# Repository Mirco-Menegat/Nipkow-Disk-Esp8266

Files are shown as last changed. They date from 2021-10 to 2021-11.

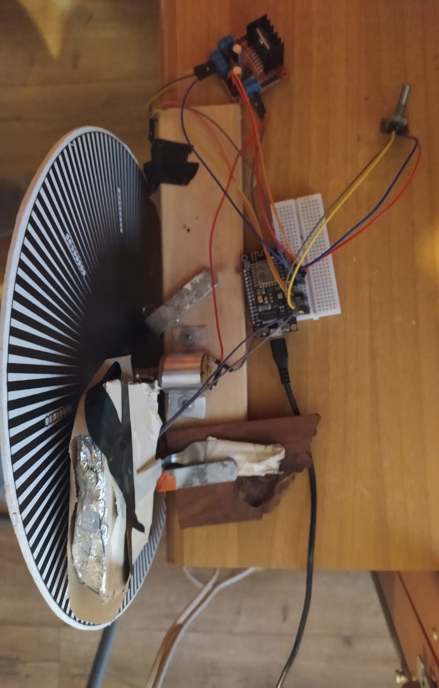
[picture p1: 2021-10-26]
img/foto_disco.jpeg

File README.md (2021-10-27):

# Nipkow-Disk-Esp8266
## Descrizione 
Rivisitazione del disco di Nipkow usando Esp8266. Il disco è in grado di proiettare immagini statiche o un testo scorrevole tramite mqtt.
È stato inserito un rotary encoder siccome solo un ottavo del disco proietta l'immagine corretta, attraverso il rotary encoder possiamo spostare la finestra in modo da averla nella giusta posizione.
Il sensore a infrarossi rileva il passaggio di 128 tacche nere e bianche poste dietro al disco. Un ottavo di queste 128 tacche determinano la risoluzione della larghezza della finestra mentre i numero di fori la risoluzione della sua altezza, quindi il disco ha una risoluzione di 16*8. I buchi e lo spazio tra una tacca e l'altra sono della dimensioni di 3 mm.
L'immagine o la scritta sono contemporaneamente proiettate sul disco e sull'interfaccia grafica in processing.
Se non è proiettata alcuna scritta, cliccando le caselle sull'interfaccia posso disegnare un'immagine.
Premendo alcuni tasti dall'interfaccia ho le seguenti funzionalità:
* 's': se è proiettata una scritta ferma/attiva lo scorrimento della stessa
* 'c': cancella lo schermo
* 'i': se non è proiettata alcuna scritta codifica l'immagine e invia messaggio mqtt all'esp8266 che la proietta sul disco.
## Materiale
* ESP8266
* Disco di Nipkow
* Motore DC 7.5V
* Motor Driver L298N
* led RGB
* Rotary Encoder
* Sensore Infrarossi

## Software ausiliario
* Processing

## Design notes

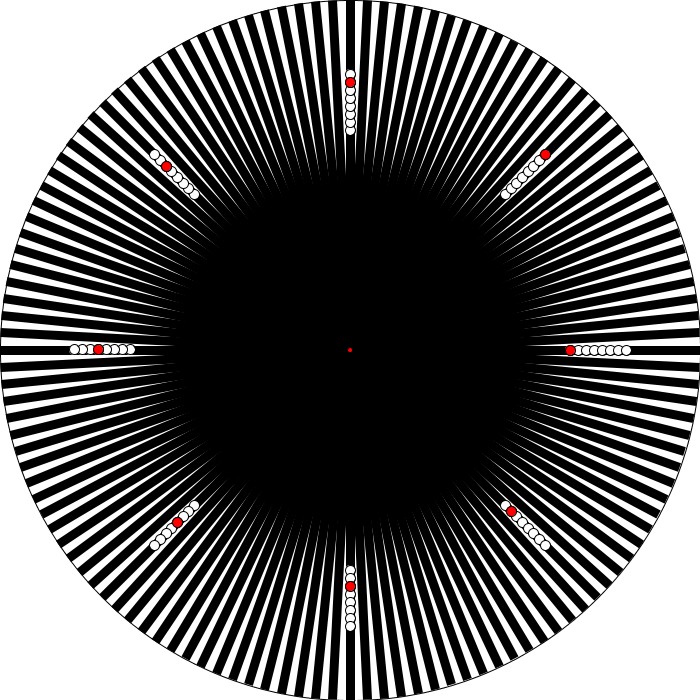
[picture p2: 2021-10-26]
img/nipkow_disk.jpeg

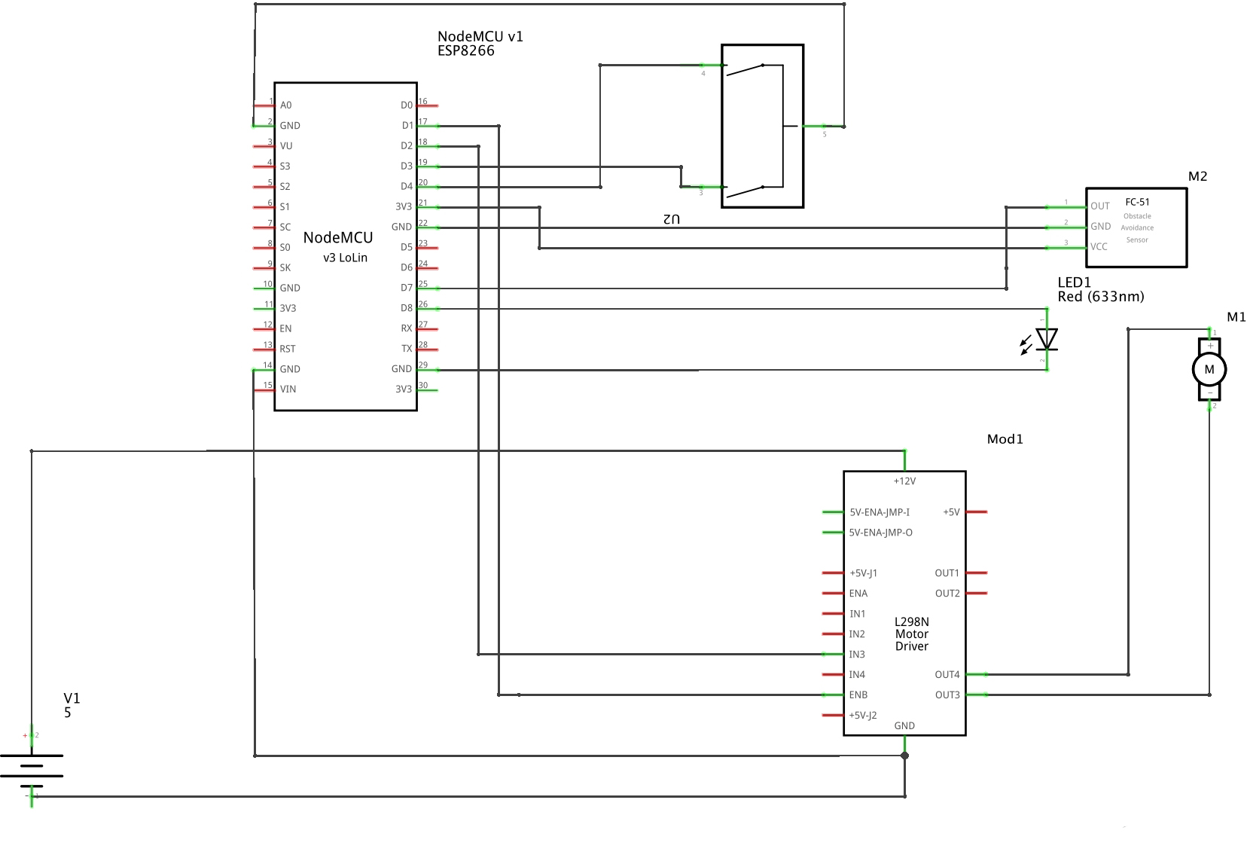
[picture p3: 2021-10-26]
Schema_Circuito.jpg

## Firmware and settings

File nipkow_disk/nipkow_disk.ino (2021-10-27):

#include <ESP8266WiFi.h>
#include <PubSubClient.h>
#include <TaskScheduler.h>
#include<stdio.h>
#include<stdlib.h>
#include <PID_v1.h>
#include "WiFi_Credenziali.h"

#define led D8
#define sensore D7
#define enB  D1
#define in3  D2
#define outputA D3 //DT
#define outputB D4 //CLK


//PID
double Setpoint=580; ; //Rpm ideali
double RPM;
double Output=0 ;
double Kp=2, Ki=10, Kd=0;
double time0_RPM;
double time1_RPM;
PID myPID(&RPM, &Output, &Setpoint, Kp, Ki, Kd, DIRECT);


//STATI DEL ROTARY ENCODER CORRENTE E PRECEDENTE  
int aState;
int aLastState;

// CREDENZIALI WIFI
const char *ssid = ssid_Wifi;
const char *password = password_Wifi;

// MQTT BROKER
const char *mqtt_broker = "broker.hivemq.com";
const char *topic = "/Nipkow_Disk-Esp8266/buffer";
const char *mqtt_username = "esp8266";
const char *mqtt_password = "public";
const int mqtt_port = 1883;

//BUFFER CORRENTE E BUFFER DI RISERVA
boolean sel_buff=false;                         //flag di selezione per selezionare il buffer corrente e quello di riserva
int buff0[128];
int buff_length=8;
int * buff_pointer=buff0;                        //puntatore al buffer corrente così da non dover spostare tutti gli elementi da un buffer all'altro ma solo il puntatore

int buff1[128];
int buff_length_riserva=8;
int nuovo_messaggio=false;                      //indica se è arrivato un nuovo messaggio mqtt

int contatore_buffer=0;                         //Indice elemento del buffer corrente
boolean luce=false;
int offset=0;
float conta_tacche=0;

Scheduler runner;
WiFiClient espClient;
PubSubClient client(espClient);

//Girando il potenziometro a destra o sinistra aumento o diminuisco rispettivamente l'offset, così da girare la finestra in senso orario o antiorario
void gestisci_rotary_encoder() {
        aState = digitalRead(outputA);
        if (aState != aLastState) {               //girando il potenziometro sposto la finestra a in senso orario o antiorario
            if (digitalRead(outputB) != aState ) { //Se ruoto il potenziometro in senso orario
                offset ++;
            } else { //Se ruoto il potenziometro in senso antiorario
                offset--;
            }
        }
       aLastState = aState;
}

//Calcola RPM del disco
void calculate_RPM() {
    if (time1_RPM-time0_RPM!=0) {
        RPM=60000/(time1_RPM-time0_RPM);       //1 minuto/ il tempo che ci mette a fare un giro
    }
}

void pid_loop(){
    myPID.Compute();
    analogWrite(enB,map(Output,0,255,0,1023));
}
void mqtt_loop(){
   client.loop();
}

void stampa() {
    Serial.println(RPM);
}
Task mqttTask(3*TASK_MILLISECOND, TASK_FOREVER,mqtt_loop);
Task pidTask(3*TASK_MILLISECOND, TASK_FOREVER, pid_loop);
Task printTask(5000*TASK_MILLISECOND, TASK_FOREVER, stampa);
Task rotary_encoderTask(10*TASK_MILLISECOND, TASK_FOREVER, gestisci_rotary_encoder);


//Inverte la luce da accesa a spenta o viceversa contatore_buffer diventa l'indice dell'elemento successivo
void inverti_luce(boolean _luce) {
    luce=!luce;
    if (contatore_buffer<buff_length-1) {
        contatore_buffer++;
    }
    switch(luce) {
    case false:
        digitalWrite(led,LOW);
        break;
    case true:
        digitalWrite(led,HIGH);
        break;
    }
}

//Inverte il buffer puntato da buff_pointer, quello di riserva diventa quello corrente e quello corrente diventa di riserva
void inverti_buffer() {
    buff_length=buff_length_riserva;
    switch(sel_buff) {
    case false:
        buff_pointer=buff0;
        break;
    case true:
        buff_pointer=buff1; ;
        break;
    }
}

//Controlla se il disco è all'inizio del giro, spegne la luce e memorizza il tempo di inizio per calcolare gli rpm
boolean check_inizio_giro() {
    if (conta_tacche==offset) {                        //Inizio il giro sempre con luce spenta
        time0_RPM=millis();
        luce=false;
        digitalWrite(led,LOW);
        return true;
    }
    return false;
}

//Controlla se il disco ha completato un giro, dopo aver memorizzato il tempo che ci ha messo a fare un giro calcola gli RPM, e riporta il disco in condizione iniziale
//Se è arrivato un nuovo messaggio mqtt inverti_buffer()
boolean check_fine_giro() {
    if (conta_tacche>=128+offset) {           //mi preparo a scrivere la nuova colonna solo quando ho finito tutto il giro
        time1_RPM=millis();
        calculate_RPM();
        conta_tacche=offset;
        contatore_buffer=0;
        if (nuovo_messaggio==true) {
            inverti_buffer();
        }
        return true;
    }
    return false;
}

//controllo se sono a inizio giro, aumento il conteggio delle tacche,se il conta_tacche coincide con con il prossimo elemento del buffer inverto la luce, controllo se ho finito
//il giro, se l'indice di elemento del buffer è >= della lunghezza del buffer lo riporto a 0.
void ICACHE_RAM_ATTR gestisci_luce() {
    check_inizio_giro();
    conta_tacche++;
    if (buff_length>0 && int(conta_tacche)==buff_pointer[buff_length-1-contatore_buffer]+offset ) { //Se il buffer non è vuoto e conta_tacche coincide con il prossimo elemento del buffer (conto dal fondo)
        inverti_luce(luce);
    }
    check_fine_giro();
    if (contatore_buffer>=buff_length) {
        contatore_buffer=0;
    }
}


// Leggo il payload dal fondo e inserisco i numeri nel buffer di riserva, quando ho finito nuovo_messagio=true e scambio e indico che il buffer di riserva sarà il prossimo
//buffer corrente
void gestisci_nuovo_messaggio(char *topic, byte *payload, unsigned int length) {
    Serial.print("Nuovo messaggio nel topic: ");
    Serial.println(topic);
    Serial.print("Messaggio:");

    int indice=1,numero=0;
    int n_elemento=0;
    for (int i = length-1; i >=0 ; i--) {  //leggo il char * al contrario così da poter ricostruire i numeri ed inserirli nel buffer che non sto usando correntemente

        if(payload[i]!=',') {
            char cifra=(char) payload[i];
            numero+=(cifra-'0')*indice;
            indice*=10;

        } else {
            switch(sel_buff) {
            case true:
                buff0[n_elemento]=numero;
                break;
            case false:
                buff1[n_elemento]=numero;
                break;
            }
            n_elemento++;
            Serial.print(numero);
            Serial.print(" ");
            indice=1;
            numero=0;
        }
    }
    buff_length_riserva=n_elemento;

    Serial.println();
    Serial.println("-----------------------");
    nuovo_messaggio=true;
    sel_buff=!sel_buff;
}

void setup() {
    Serial.begin(115200);
    pinMode(enB, OUTPUT);
    pinMode(in3, OUTPUT);
    pinMode(led,OUTPUT);
    pinMode(sensore,INPUT_PULLUP);
    Serial.begin (115200);
    digitalWrite(in3, HIGH);

    attachInterrupt(
        digitalPinToInterrupt(sensore),
        gestisci_luce,
        RISING
    );
    // connecting to a WiFi network
    WiFi.begin(ssid, password);
    while (WiFi.status() != WL_CONNECTED) {
        delay(400);
        Serial.println("Connecting to WiFi..");
    }
    Serial.println("Connected to the WiFi network");

    //connecting to a mqtt broker
    client.setServer(mqtt_broker, mqtt_port);
    client.setCallback(gestisci_nuovo_messaggio);
    while (!client.connected()) {
        String client_id = "esp8266-client-";
        client_id += String(WiFi.macAddress());
        Serial.printf("The client %s connects to mqtt broker\n", client_id.c_str());
        if (client.connect(client_id.c_str(), mqtt_username, mqtt_password)) {
            Serial.println("Connected to mqtt broker");
        } else {
            Serial.print("failed with state ");
            Serial.print(client.state());
            delay(100);

        }
    }

    client.subscribe(topic);

    runner.init();
    runner.addTask(printTask);
    runner.addTask(rotary_encoderTask);
    runner.addTask(pidTask);
    runner.addTask(mqttTask);
    mqttTask.enable();
    pidTask.enable();
    printTask.enable();
    rotary_encoderTask.enable();
    aLastState = digitalRead(outputA);

    myPID.SetMode(AUTOMATIC);
    //Adjust PID values
    myPID.SetTunings(Kp, Ki, Kd);
}

void loop() {
    runner.execute();
}

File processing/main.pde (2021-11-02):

import mqtt.*;
import java.nio.charset.StandardCharsets;
int pausa_messaggio=1000;
byte [] stringa=null;
boolean scorri=true;
int altezza =8;
int lunghezza=16;
color bianco=color (255);
color rosso=color (255,0,0);
color [] colori={bianco,rosso};
int iterazione;
float time1=0;
int numero_lettera=0;                                                            //indice lettera nella parola
int lunghezza_lettera=0;                                                         //indice colonna della lettera
int transla_count=0;                                                             //quando finisco di scrivere la parola conta le traslazioni finche non è sparita dallo schermo
int Lettera[][]={{}}; 
MQTTClient client;
TEXTBOX userTB;

grid g;


int A[][]={{15,31,47,63,79,95,111,127},{63,127},{63,127},{15,31,47,63,79,95,111,127}};
int B[][]={{15,31,47,63,79,95,111,127},{15,79,127},{15,79,127},{15,31,47,63,95,111,127}};
int C[][]={{15,31,47,63,79,95,111,127},{15,127},{15,127},{15,127}};
int D[][]={{15,31,47,63,79,95,111,127},{15,127},{15,127},{31,47,63,79,95,111}};
int E[][]={{15,31,47,63,79,95,111,127},{15,63,127},{15,63,127},{15,127}};
int F[][]={{15,31,47,63,79,95,111,127},{63,127},{63,127},{127}};
int G[][]={{15,31,47,63,79,95,111,127},{15,127},{15,63,127},{15,31,47,63,127}};
int H[][]={{15,31,47,63,79,95,111,127},{63},{63},{15,31,47,63,79,95,111,127}};
int I[][]={{15,31,47,63,79,95,111,127}};
int J[][]={{15,31,47},{15},{15},{15,31,47,63,79,95,111,127}};
int K[][]={{15,31,47,63,79,95,111,127},{63,95},{47,111},{15,31,127}};
int L[][]={{15,31,47,63,79,95,111,127},{15},{15},{15}};
int M[][]={{15,31,47,63,79,95,111,127},{127},{95,111,127},{127},{15,31,47,63,79,95,111,127}};
int N[][]={{15,31,47,63,79,95,111,127},{111},{95},{79},{15,31,47,63,79,95,111,127}};
int O[][]={{15,31,47,63,79,95,111,127},{15,127},{15,127},{15,31,47,63,79,95,111,127}};
int P[][]={{15,31,47,63,79,95,111,127},{79,127},{79,127},{79,95,111,127}};
int Q[][]={{15,31,47,63,79,95,111,127},{15,127},{15,127},{15,31,47,63,79,95,111,127},{15}};
int R[][]={{15,31,47,63,79,95,111,127},{63,79,127},{47,79,127},{15,31,79,95,111,127}};
int S[][]={{15,79,95,111,127},{15,79,127},{15,79,127},{15,31,47,63,79,127}};
int T[][]={{127},{127},{15,31,47,63,79,95,111,127},{127},{127}};
int U[][]={{15,31,47,63,79,95,111,127},{15},{15},{15,31,47,63,79,95,111,127}};
int V[][]={{47,63,79,95,111,127},{31},{15},{31},{47,63,79,95,111,127}};
int W[][]={{15,31,47,63,79,95,111,127},{15},{15,31,47},{15},{15,31,47,63,79,95,111,127}};
int X[][]={{15,31,47,111,127},{63,95},{79},{63,95},{15,31,47,111,127}};
int Y[][]={{111,127},{95},{15,31,47,63,79},{95},{111,127}};
int Z[][]={{15,31,127},{15,47,127},{15,63,127},{15,79,127},{15,95,111,127}};
int NR[][]={{95,111},{127},{15,47,63,127},{79,127},{95,111}}; //carattere non riconosciuto -> ?

void update(){ //Preparo la griglia alla prossima colonna da inserire
         switch(stringa[numero_lettera]){
                case 'A':Lettera=A;break;
                case 'B':Lettera=B;break;
                case 'C':Lettera=C;break;
                case 'D':Lettera=D;break;
                case 'E':Lettera=E;break;
                case 'F':Lettera=F;break;
                case 'G':Lettera=G;break;
                case 'H':Lettera=H;break;
                case 'I':Lettera=I;break;
                case 'J':Lettera=J;break;
                case 'K':Lettera=K;break;
                case 'L':Lettera=L;break;
                case 'M':Lettera=M;break;
                case 'N':Lettera=N;break;
                case 'O':Lettera=O;break;
                case 'P':Lettera=P;break;
                case 'Q':Lettera=Q;break;
                case 'R':Lettera=R;break;
                case 'S':Lettera=S;break;
                case 'T':Lettera=T;break;
                case 'U':Lettera=U;break;
                case 'V':Lettera=V;break;
                case 'W':Lettera=W;break;
                case 'X':Lettera=X;break;
                case 'Y':Lettera=Y;break;
                case 'Z':Lettera=Z;break;
                default:Lettera=NR;break;
           }
        
              for(int i=0;i<Lettera[lunghezza_lettera].length;i++){
                   g.griglia[Lettera[lunghezza_lettera][i]].col=rosso;
               }      
              
}

void setup(){
 background(0,180,180);
  client = new MQTTClient(this);
  client.connect("mqtt://broker.hivemq.com", "processing");
  size(800,500);
 g =new grid(16,8);
 g.draw_griglia();
   userTB = new TEXTBOX();
   userTB.X = 250;
   userTB.Y = 430;
   userTB.W = 200;
   userTB.H = 35;


}

void draw(){
   
   if(millis()-time1>pausa_messaggio){       
     //background(180,180,40);
      if(scorri==true && stringa!=null){        
          if (transla_count==lunghezza-1){
              numero_lettera=0;
              lunghezza_lettera=0;
              transla_count=0;
          }
          if (numero_lettera<stringa.length){
              if (lunghezza_lettera<Lettera.length){
                  update();
                  lunghezza_lettera++;
              }else{
                  numero_lettera++;
                  lunghezza_lettera=0;
              }
          }else{
              transla_count++;
          }
     g.draw_griglia();
     invia();
     g.transla(); 
     time1=millis();
     }else if(stringa==null){
         g.draw_griglia();
    }
    fill(250, 250, 250);
   textSize(25);
   text("INVIA MESSAGGIO", 20, 455);
   userTB.DRAW();

   strokeWeight(3);
   textSize(12);
   }
   
  
   
}



void invia(){
String codifica_stringa="";
if (g.griglia[0].col==rosso){
    codifica_stringa= codifica_stringa+",";
    codifica_stringa=codifica_stringa+Integer.toString(1);
}
for(int i=1;i<g.altezza*g.larghezza;i++){
  if (g.griglia[i].col!=g.griglia[i-1].col){
    codifica_stringa=codifica_stringa+",";
    codifica_stringa=codifica_stringa+Integer.toString(i+1);}
}
 println(codifica_stringa);
 println();
 client.publish("/Nipkow_Disk-Esp8266/buffer", codifica_stringa);
}


void clientConnected() {
  println("client connected");
  client.subscribe("/Nipkow_Disk-Esp8266/processing");
}

void connectionLost() {
  println("connection lost");
}

void messageReceived(String topic, byte[] payload) {
  transla_count=0;
  lunghezza_lettera=0;
  numero_lettera=0;
  scorri=true;
  String s = new String(payload, StandardCharsets.UTF_8);
  s=s.toUpperCase();
  stringa=s.getBytes();
  for (int i=0;i<g.altezza*g.larghezza;i++){
    g.griglia[i].col=bianco;
  }
  println("nuovo messaggio: " + topic + " - " + new String(stringa));
}

void mousePressed() {
  
     userTB.PRESSED(mouseX, mouseY);
     if (stringa==null){
     for (int i=0;i<g.altezza*g.larghezza;i++){
    g.griglia[i].PRESSED(mouseX,mouseY);
     }}
}
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

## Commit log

2021-10-26 Add files via upload
    Schema circuitale
    [Circuito.fzz]
2021-10-26 Schema circuitale
2021-10-26 Modularizzato il codice delle funzioni
2021-10-27 Eliminato time_0 encoder
    Il bounce viene eliminato direttamente usando il task scheduler
